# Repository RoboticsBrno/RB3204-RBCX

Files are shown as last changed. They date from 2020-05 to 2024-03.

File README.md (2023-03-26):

# RB3204-RBCX

<p align="center">




</p>

RBCX is a universal controller for hobby robots. It is a successor of [RB3201-RBControl](https://github.com/RoboticsBrno/RB3201-RBControl).
It is used in our robot [Robotka](https://robotka.robotickytabor.cz) on [Robo camp 2020](https://robotickytabor.cz).

<div align="center">
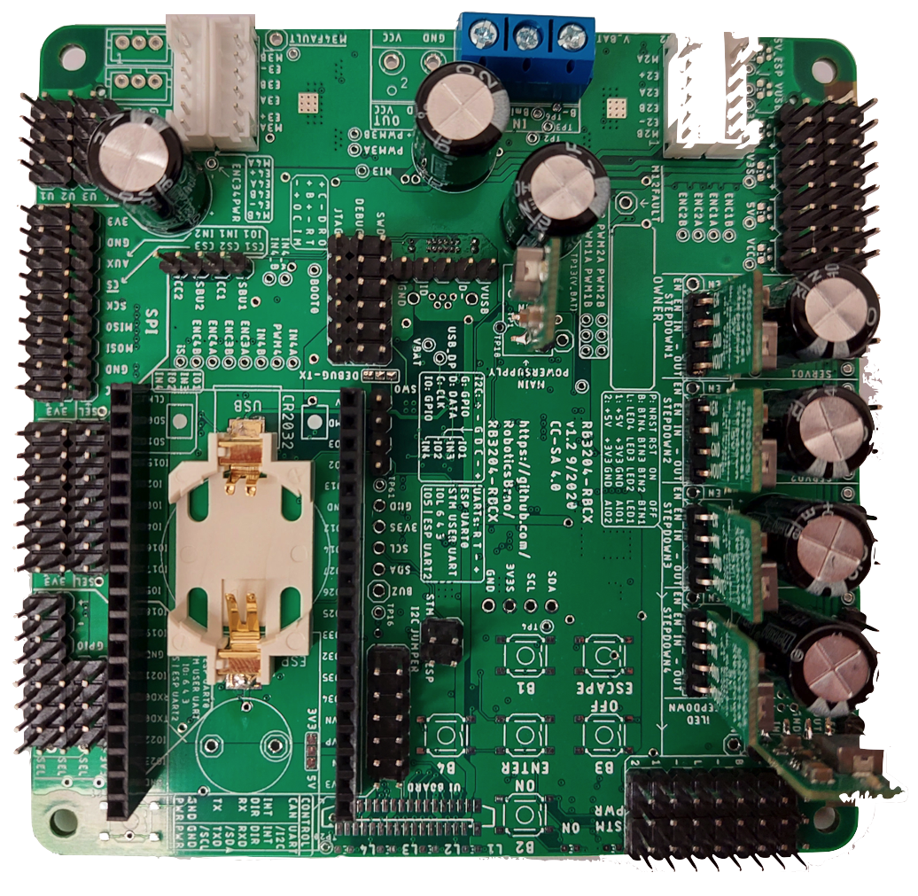
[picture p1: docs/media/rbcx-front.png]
  	<td></td>
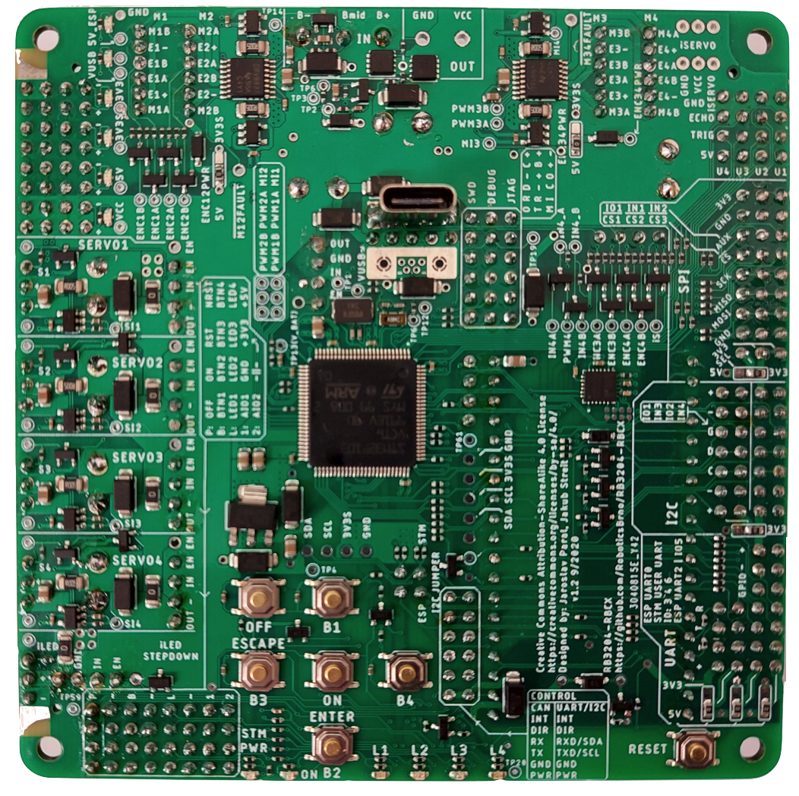
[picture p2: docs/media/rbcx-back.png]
	<td></td>
</div>

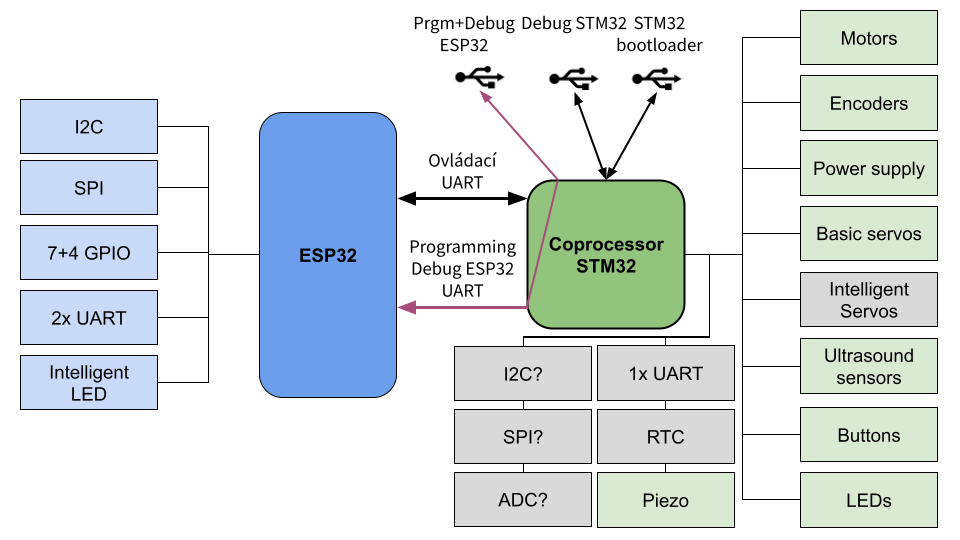
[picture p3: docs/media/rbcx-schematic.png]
RBCX


## Features
- 4 DC motors with encoders
- 4 servos with feedback (via ADC)
- 4 LEDs
- buttons with the gamepad interface
- Smart Servo connector
- piezo buzzer
- RTC
- ultra-sonic distance sensor connector
- I2C connectors
- OLED display connector
- accelerometer and gyroscope
- micro USB and USB-C connectors
- battery connector (without charging circuit)

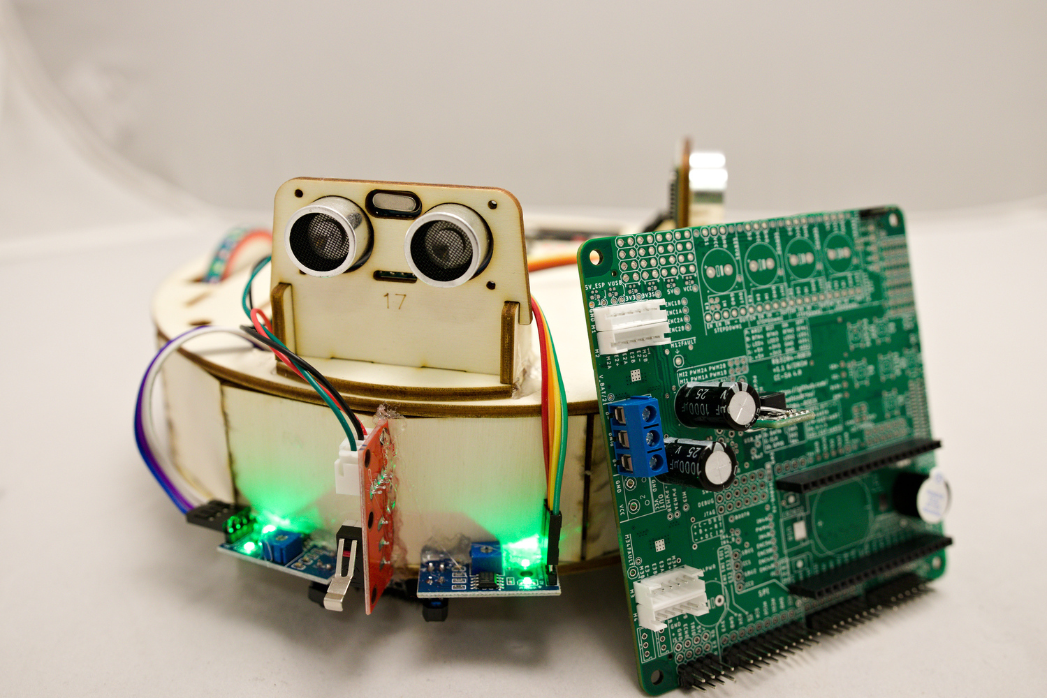
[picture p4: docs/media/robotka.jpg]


## Hardware
Board is based on `STM32F103VC` microcontroller and `ESP32-DevKitC`.

STM32 is used for motor control and other low-level tasks.
ESP32 is used for high-level tasks like communication with mobile app and sending commands to STM32 via UART.

### [STM32F103VC](https://www.st.com/en/microcontrollers-microprocessors/stm32f103vc.html)

-  72 MHz, 32bit ARM Cortex-M3
-  48 KiB RAM, 256 KiB Flash
-  5x UART, USB
-  Debug support (with ST-Link)
-  Programmable in C++, with FreeRTOS and stm32cube framework, in Platform.io
-  Our [bootloader](https://github.com/RoboticsBrno/sboot_stm32) based on [sboot_stm32](https://github.com/dmitrystu/sboot_stm32).

### [ESP32-DevKitC](https://www.espressif.com/en/products/devkits/esp32-devkitc)

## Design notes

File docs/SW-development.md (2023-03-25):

# Software development
Both microcontrollers are programmed using [PlatformIO](https://platformio.org/) in [VSCode](https://code.visualstudio.com/) using C++ language.

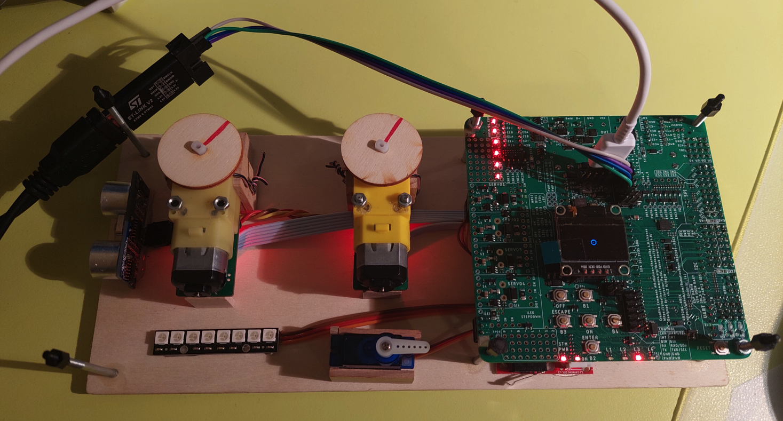
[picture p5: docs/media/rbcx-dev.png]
RBCX development


## STM32
The software for STM32 is located in `fw` directory.
STM32 uses our [bootloader](https://github.com/RoboticsBrno/sboot_stm32), which is based on [sboot_stm32](https://github.com/dmitrystu/sboot_stm32).

The Czech manuals are in these presentations:
- [RBCX](https://docs.google.com/presentation/d/1NP2yii9ZfLh_otC2qz9LTG4m3adRt0aGy-u8AYXcY6M/)
- [RBCX firmware](https://docs.google.com/presentation/d/1B4t7tvKhTz8Nwm9SQEp_2enkG-x4il2hApb1tdSRLiI)

### Bootloader installation
RBCX might work without bootloader, but it is not recommended. Thanls to the bootloader, you can program STM32 without STLink programmer and program ESP32 directly trough USB-C in RBCX.

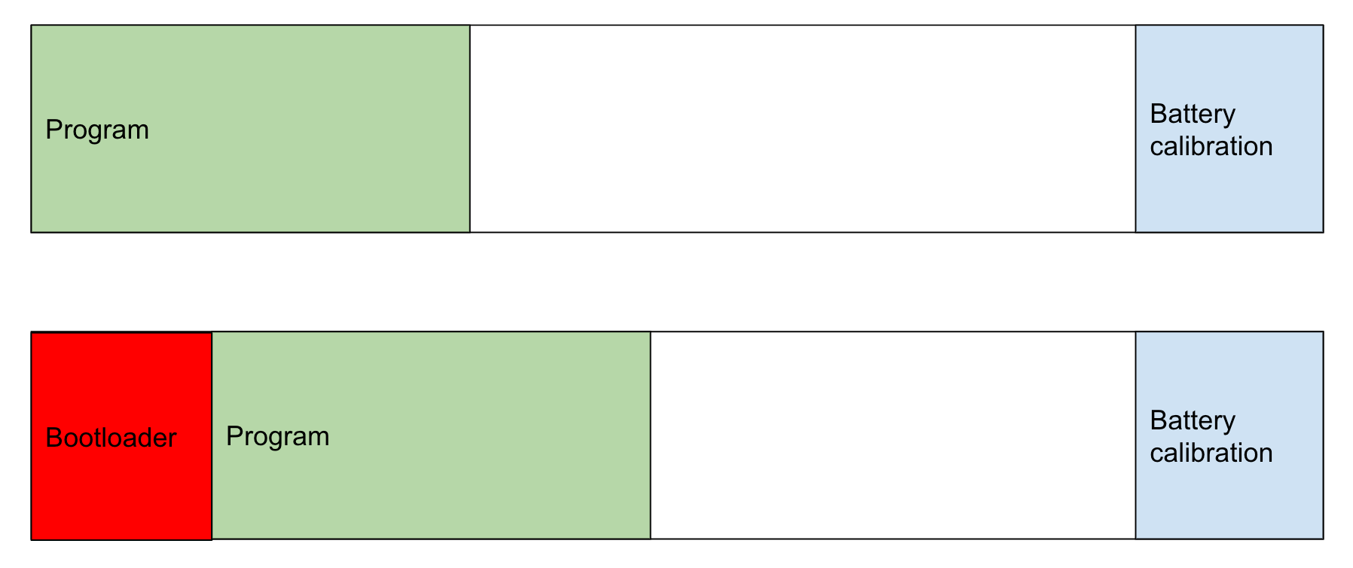
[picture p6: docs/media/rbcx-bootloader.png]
RBCX bootloader


- you need STLink programmer
  - connect STLink programmer to the board→
    - C → SWCLK
    - -→ GND
    - D → SWDIO
    - R → RST
    - +→ 3.3V (optional, if you want to power the board from STLink)
  - !! If STLink is not connected to the computer, STM32 is in a reset state !!
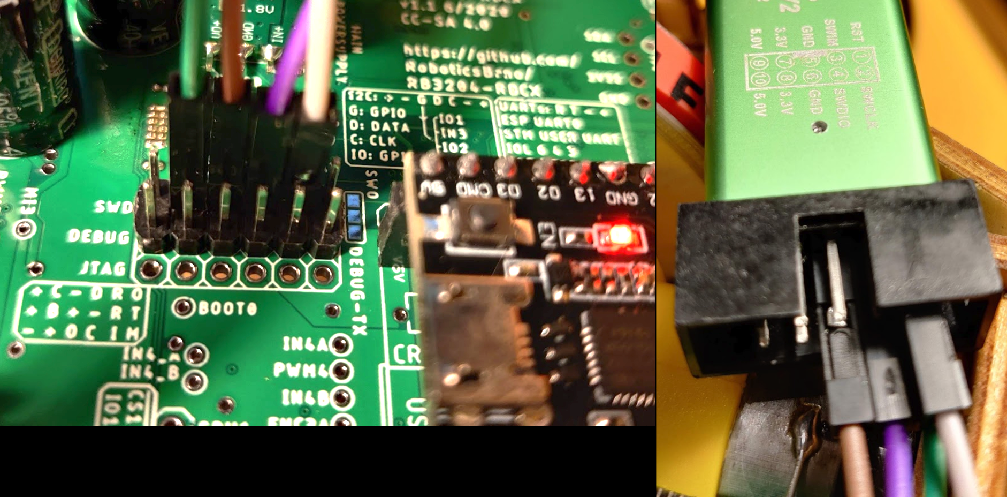
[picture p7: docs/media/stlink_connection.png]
STLink connection
  - 

- clone `https://github.com/RoboticsBrno/sboot_stm32`
- `apt-get install stlink-tools make gcc-arm-none-eabi git`
- flash prebuilt bootloader `st-flash --reset --format ihex write prebuilt/rbcx_v11/firmware.hex`
- compile and flash firmware `make prerequisites && ./rbcx_build_v11.sh && make program`

### Firmware installation
Firmware for STM32 is located in `fw/rbcx-coprocessor` directory.
RBCX might be programmed using STLink programmer or using USB-C connector.

### STLink development
In VSCode - PlatformIO, you have to change the environment to `hw*_stlink`.
This setup supports debugging. Just press `F5` or `Debug` button in VSCode.

### USB C development
If you want to use USB-C connector for programming STM32, you need to press `DOWN` button (B2) on the board during the boot.
In default mode, USB-C connector is used for communication with ESP32.

To enable Debug output from STM32, you have to press `LEFT` button (B3) on the board during the boot. This will add virtual debug serial port to the USB-C connector.

STM32 will create two virtual COM ports (one for STM32 and one for ESP32).
In VSCode - PlatformIO, you have to change the environment to `hw*_sboot`.
This setup does not support debugging (use STLink programmer for debugging).

## ESP32
The library for ESP32 is in [RB3204-RBCX-library](https://github.com/RoboticsBrno/RB3204-RBCX-library) repository.
Examples for the [Robotka](https://robotka.robotickytabor.cz), which is a robot based on RBCX, are in [robotka-examples](https://github.com/RoboticsBrno/robotka-examples) repository.

RBCX

## Programming ESP32
STM32 behaves like "FTDI" on dev kit, so you can program ESP32 using USB-C connector.

- Controls boot pins on ESP32 according to RTS/DTR.
- It supports faster UART than ESP32 DevKit (faster programming)
- ESP32 DevKit cannot be programmed via its own USB while plugged into RBCX

## ESP32 and STM32 communication
ESP32 and STM32 communicate via UART (baud 921600)

Microcontrollers are communicating using [Protocol Buffers](https://developers.google.com/protocol-buffers) (Protobuf).
Protobuf messages are defined in [RB3204-RBCX-coproc-comm](https://github.com/RoboticsBrno/RB3204-RBCX-coproc-comm) repository.

### Commands
"Run motor at 50%", "Battery voltage is 6802mV", "Reset the board"

Protocol: [Protobuf](https://protobuf.dev/) + [COBS](https://en.wikipedia.org/wiki/Consistent_Overhead_Byte_Stuffing) + small header

- `0x00, <length>, <data>`

Keepalive - when ESP32 does not respond, it is reset, STM32 turns off peripherals

### Installation and usage
- clone `https://github.com/RoboticsBrno/RB3204-RBCX-coproc-comm`
- install protobuf compiler `apt-get install protobuf-compiler`
- install nanopb generator `pip3 install nanopb==0.4.4`
- edit `rbcx.proto` file
- compile protobuf messages using `./generate.sh`
- commit and push changes to GitHub
- change GIT hash in FW and RBCX library to the latest commit hash

## Schematic
RBCX

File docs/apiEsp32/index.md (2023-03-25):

# API ESP-32

This is the API documentation for the [ESP32-DevKitC](https://www.espressif.com/en/products/devkits/esp32-devkitc) microcontroller.

## Firmware

More information about firmware can be found in [SW Development](../SW-development.md) section.

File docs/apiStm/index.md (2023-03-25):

# API STM32

This is the API documentation for the [STM32F103VC](https://www.st.com/en/microcontrollers-microprocessors/stm32f103vc.html) microcontroller.

## Firmware

More information about firmware can be found in [SW Development](../SW-development.md) section.

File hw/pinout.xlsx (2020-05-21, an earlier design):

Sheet: koprocesor
pin LQFP100 | 5V TOLERANT | GPIO | TIMER1 |  |  | TIMER2 |  |  |  | TIMER3 |  |  | TIMER4 |  | TIMER5 | TIMER8 | USART1 |  | USART2 |  | USART3 |  |  | UART4 | UART5 | CAN1 |  |  | I2C1 |  | I2C2 | SPI1 |  | SPI2 | SPI3 |  | USB | SDIO | DAC | ADC1 | ADC2 | ADC3 | JTAG/SWD | AUX | Periferie | Signal | Note
 |  | remap: | 00 | 01 | 11 | 00 | 01 | 10 | 11 | 00 | 10 | 11 | 0 | 1 |  |  | 0 | 1 | 0 | 1 | 00 | 01 | 11 |  |  | 00 | 10 | 11 | 0 | 1 |  | 0 | 1 |  | 0 | 1
1 |  | PE2 |  |  |  |  |  |  |  |  |  |  |  |  |  |  |  |  |  |  |  |  |  |  |  |  |  |  |  |  |  |  |  |  |  |  |  |  |  |  |  |  |  |  | PE2 | UTS2_TRIG
2 |  | PE3 |  |  |  |  |  |  |  |  |  |  |  |  |  |  |  |  |  |  |  |  |  |  |  |  |  |  |  |  |  |  |  |  |  |  |  |  |  |  |  |  |  |  | PE3 | UTS2_ECHO
3 |  | PE4 |  |  |  |  |  |  |  |  |  |  |  |  |  |  |  |  |  |  |  |  |  |  |  |  |  |  |  |  |  |  |  |  |  |  |  |  |  |  |  |  |  |  | PE4 | UTS3_TRIG
4 |  | PE5 |  |  |  |  |  |  |  |  |  |  |  |  |  |  |  |  |  |  |  |  |  |  |  |  |  |  |  |  |  |  |  |  |  |  |  |  |  |  |  |  |  |  | PE5 | UTS3_ECHO
5 |  | PE6 |  |  |  |  |  |  |  |  |  |  |  |  |  |  |  |  |  |  |  |  |  |  |  |  |  |  |  |  |  |  |  |  |  |  |  |  |  |  |  |  |  |  | PE6 | UTS4_TRIG
6 |  | VBAT |  |  |  |  |  |  |  |  |  |  |  |  |  |  |  |  |  |  |  |  |  |  |  |  |  |  |  |  |  |  |  |  |  |  |  |  |  |  |  |  |  |  | VBAT | VBAT
7 | LI+S | PC13 |  |  |  |  |  |  |  |  |  |  |  |  |  |  |  |  |  |  |  |  |  |  |  |  |  |  |  |  |  |  |  |  |  |  |  |  |  |  |  |  |  | RTC_TAMPER | PC13 | VUSB_DET
8 | LI+S | PC14 |  |  |  |  |  |  |  |  |  |  |  |  |  |  |  |  |  |  |  |  |  |  |  |  |  |  |  |  |  |  |  |  |  |  |  |  |  |  |  |  |  | OSC32_IN | OSC32_IN | OSC 32 kHz
9 | LI+S | PC15 |  |  |  |  |  |  |  |  |  |  |  |  |  |  |  |  |  |  |  |  |  |  |  |  |  |  |  |  |  |  |  |  |  |  |  |  |  |  |  |  |  | OSC32_OUT | OSC32_OUT | OSC 32 kHz
10 |  | VSS |  |  |  |  |  |  |  |  |  |  |  |  |  |  |  |  |  |  |  |  |  |  |  |  |  |  |  |  |  |  |  |  |  |  |  |  |  |  |  |  |  |  | VSS | VSS
11 |  | VDD |  |  |  |  |  |  |  |  |  |  |  |  |  |  |  |  |  |  |  |  |  |  |  |  |  |  |  |  |  |  |  |  |  |  |  |  |  |  |  |  |  |  | VDD | VDD
12 |  | OSC_IN |  |  |  |  |  |  |  |  |  |  |  |  |  |  |  |  |  |  |  |  |  |  |  |  |  |  |  |  |  |  |  |  |  |  |  |  |  |  |  |  |  |  | OSC_IN | OSC_IN
13 |  | OSC_OUT |  |  |  |  |  |  |  |  |  |  |  |  |  |  |  |  |  |  |  |  |  |  |  |  |  |  |  |  |  |  |  |  |  |  |  |  |  |  |  |  |  |  | OSC_OUT | OSC_OUT
14 |  | NRST |  |  |  |  |  |  |  |  |  |  |  |  |  |  |  |  |  |  |  |  |  |  |  |  |  |  |  |  |  |  |  |  |  |  |  |  |  |  |  |  |  |  | NRST | NRST
15 |  | PC0 |  |  |  |  |  |  |  |  |  |  |  |  |  |  |  |  |  |  |  |  |  |  |  |  |  |  |  |  |  |  |  |  |  |  |  |  |  | IN10 | IN10 | IN10 |  |  | ADC3_IN10 | SI1
16 |  | PC1 |  |  |  |  |  |  |  |  |  |  |  |  |  |  |  |  |  |  |  |  |  |  |  |  |  |  |  |  |  |  |  |  |  |  |  |  |  | IN11 | IN11 | IN11 |  |  | ADC3_IN11 | SI2
17 |  | PC2 |  |  |  |  |  |  |  |  |  |  |  |  |  |  |  |  |  |  |  |  |  |  |  |  |  |  |  |  |  |  |  |  |  |  |  |  |  | IN12 | IN12 | IN12 |  |  | ADC3_IN12 | SI3
18 |  | PC3 |  |  |  |  |  |  |  |  |  |  |  |  |  |  |  |  |  |  |  |  |  |  |  |  |  |  |  |  |  |  |  |  |  |  |  |  |  | IN13 | IN13 | IN13 |  |  | ADC3_IN13 | SI4
19 |  | VSSA |  |  |  |  |  |  |  |  |  |  |  |  |  |  |  |  |  |  |  |  |  |  |  |  |  |  |  |  |  |  |  |  |  |  |  |  |  |  |  |  |  |  | VSSA | VSSA
20 |  | VREF- |  |  |  |  |  |  |  |  |  |  |  |  |  |  |  |  |  |  |  |  |  |  |  |  |  |  |  |  |  |  |  |  |  |  |  |  |  |  |  |  |  |  | VREF- | VREF-
21 |  | VREF+ |  |  |  |  |  |  |  |  |  |  |  |  |  |  |  |  |  |  |  |  |  |  |  |  |  |  |  |  |  |  |  |  |  |  |  |  |  |  |  |  |  |  | VREF+ | VREF+
22 |  | VDDA |  |  |  |  |  |  |  |  |  |  |  |  |  |  |  |  |  |  |  |  |  |  |  |  |  |  |  |  |  |  |  |  |  |  |  |  |  |  |  |  |  |  | VDDA | VDDA
23 |  | PA0 |  |  |  | CH1_ETR |  | CH1_ETR |  |  |  |  |  |  | CH1 |  |  |  | CTS |  |  |  |  |  |  |  |  |  |  |  |  |  |  |  |  |  |  |  |  | IN0 | IN0 | IN0 |  | WKUP | TIM5_CH1 | SERVO1
24 |  | PA1 |  |  |  | CH2 |  | CH2 |  |  |  |  |  |  | CH2 |  |  |  | RTS |  |  |  |  |  |  |  |  |  |  |  |  |  |  |  |  |  |  |  |  | IN1 | IN1 | IN1 |  |  | TIM5_CH2 | SERVO2
25 |  | PA2 |  |  |  | CH3 | CH3 |  |  |  |  |  |  |  | CH3 |  |  |  | TX |  |  |  |  |  |  |  |  |  |  |  |  |  |  |  |  |  |  |  |  | IN2 | IN2 | IN2 |  |  | TIM5_CH3 | SERVO3
26 |  | PA3 |  |  |  | CH4 | CH4 |  |  |  |  |  |  |  | CH4 |  |  |  | RX |  |  |  |  |  |  |  |  |  |  |  |  |  |  |  |  |  |  |  |  | IN3 | IN3 | IN3 |  |  | TIM5_CH4 | SERVO4
27 |  | VSS |  |  |  |  |  |  |  |  |  |  |  |  |  |  |  |  |  |  |  |  |  |  |  |  |  |  |  |  |  |  |  |  |  |  |  |  |  |  |  |  |  |  | VSS | VSS
28 |  | VDD |  |  |  |  |  |  |  |  |  |  |  |  |  |  |  |  |  |  |  |  |  |  |  |  |  |  |  |  |  |  |  |  |  |  |  |  |  |  |  |  |  |  | VDD | VDD
29 |  | PA4 |  |  |  |  |  |  |  |  |  |  |  |  |  |  |  |  | CK |  |  |  |  |  |  |  |  |  |  |  |  | NSS |  |  |  | NSS |  |  | OUT1 | IN4 | IN4 |  |  |  | DAC1/ADC2_IN4 | AIO4
30 |  | PA5 |  |  |  |  |  |  |  |  |  |  |  |  |  |  |  |  |  |  |  |  |  |  |  |  |  |  |  |  |  | SCK |  |  |  |  |  |  | OUT2 | IN5 | IN5 |  |  |  | DAC2/ADC2_IN5 | AIO5
31 |  | PA6 |  | BKIN |  |  |  |  |  | CH1 |  |  |  |  |  | BKIN |  |  |  |  |  |  |  |  |  |  |  |  |  |  |  | MISO |  |  |  |  |  |  |  | IN6 | IN6 |  |  |  | ADC2_IN6 | VBAT
32 |  | PA7 |  | CH1N |  |  |  |  |  | CH2 |  |  |  |  |  | CH1N |  |  |  |  |  |  |  |  |  |  |  |  |  |  |  | MOSI |  |  |  |  |  |  |  | IN7 | IN7 |  |  |  | ADC2_IN7 | VBAT/2
33 |  | PC4 |  |  |  |  |  |  |  |  |  |  |  |  |  |  |  |  |  |  |  |  |  |  |  |  |  |  |  |  |  |  |  |  |  |  |  |  |  | IN14 | IN14 |  |  |  | ADC1_IN14 | MI1
34 |  | PC5 |  |  |  |  |  |  |  |  |  |  |  |  |  |  |  |  |  |  |  |  |  |  |  |  |  |  |  |  |  |  |  |  |  |  |  |  |  | IN15 | IN15 |  |  |  | ADC1_IN15 | MI2
35 |  | PB0 |  | CH2N |  |  |  |  |  | CH3 | CH3 |  |  |  |  | CH2N |  |  |  |  |  |  |  |  |  |  |  |  |  |  |  |  |  |  |  |  |  |  |  | IN8 | IN8 |  |  |  | ADC1_IN8 | MI3
36 |  | PB1 |  | CH3N |  |  |  |  |  | CH4 | CH4 |  |  |  |  | CH3N |  |  |  |  |  |  |  |  |  |  |  |  |  |  |  |  |  |  |  |  |  |  |  | IN9 | IN9 |  |  |  | ADC1_IN9 | MI4
37 |  | PB2 |  |  |  |  |  |  |  |  |  |  |  |  |  |  |  |  |  |  |  |  |  |  |  |  |  |  |  |  |  |  |  |  |  |  |  |  |  |  |  |  |  | BOOT1 | PB2 | BUTTON3
38 |  | PE7 |  |  | ETR |  |  |  |  |  |  |  |  |  |  |  |  |  |  |  |  |  |  |  |  |  |  |  |  |  |  |  |  |  |  |  |  |  |  |  |  |  |  |  | PE7 | UTS4_ECHO
39 |  | PE8 |  |  | CH1N |  |  |  |  |  |  |  |  |  |  |  |  |  |  |  |  |  |  |  |  |  |  |  |  |  |  |  |  |  |  |  |  |  |  |  |  |  |  |  | CH1N | PWM1B
40 |  | PE9 |  |  | CH1 |  |  |  |  |  |  |  |  |  |  |  |  |  |  |  |  |  |  |  |  |  |  |  |  |  |  |  |  |  |  |  |  |  |  |  |  |  |  |  | CH1 | PWM1A
41 |  | PE10 |  |  | CH2N |  |  |  |  |  |  |  |  |  |  |  |  |  |  |  |  |  |  |  |  |  |  |  |  |  |  |  |  |  |  |  |  |  |  |  |  |  |  |  | CH2N | PWM2B
42 |  | PE11 |  |  | CH2 |  |  |  |  |  |  |  |  |  |  |  |  |  |  |  |  |  |  |  |  |  |  |  |  |  |  |  |  |  |  |  |  |  |  |  |  |  |  |  | CH2 | PWM2A
43 |  | PE12 |  |  | CH3N |  |  |  |  |  |  |  |  |  |  |  |  |  |  |  |  |  |  |  |  |  |  |  |  |  |  |  |  |  |  |  |  |  |  |  |  |  |  |  | CH3N | PWM3B
44 |  | PE13 |  |  | CH3 |  |  |  |  |  |  |  |  |  |  |  |  |  |  |  |  |  |  |  |  |  |  |  |  |  |  |  |  |  |  |  |  |  |  |  |  |  |  |  | CH3 | PWM3A
45 |  | PE14 |  |  | CH4 |  |  |  |  |  |  |  |  |  |  |  |  |  |  |  |  |  |  |  |  |  |  |  |  |  |  |  |  |  |  |  |  |  |  |  |  |  |  |  | CH4 | PWM4
46 |  | PE15 |  |  | BKIN |  |  |  |  |  |  |  |  |  |  |  |  |  |  |  |  |  |  |  |  |  |  |  |  |  |  |  |  |  |  |  |  |  |  |  |  |  |  |  | PE15/TIM1_BKIN | BUTTON_ESC/OFF
47 |  | PB10 |  |  |  |  |  | CH3 | CH3 |  |  |  |  |  |  |  |  |  |  |  | TX |  |  |  |  |  |  |  |  |  | SCL |  |  |  |  |  |  |  |  |  |  |  |  |  | I2C2_SCL | I2C_SCL
48 |  | PB11 |  |  |  |  |  | CH4 | CH4 |  |  |  |  |  |  |  |  |  |  |  | RX |  |  |  |  |  |  |  |  |  | SDA |  |  |  |  |  |  |  |  |  |  |  |  |  | I2C2_SDA | I2C_SDA
49 |  | VSS |  |  |  |  |  |  |  |  |  |  |  |  |  |  |  |  |  |  |  |  |  |  |  |  |  |  |  |  |  |  |  |  |  |  |  |  |  |  |  |  |  |  | VSS | VSS
50 |  | VDD |  |  |  |  |  |  |  |  |  |  |  |  |  |  |  |  |  |  |  |  |  |  |  |  |  |  |  |  |  |  |  |  |  |  |  |  |  |  |  |  |  |  | VDD | VDD
51 |  | PB12 | BKIN |  |  |  |  |  |  |  |  |  |  |  |  |  |  |  |  |  | CK |  |  |  |  |  |  |  |  |  | SMBA |  |  | NSS |  |  |  |  |  |  |  |  |  |  | SPI2_NSS | SPI/ESP_JTAG
52 |  | PB13 | CH1N |  |  |  |  |  |  |  |  |  |  |  |  |  |  |  |  |  | CTS | CTS |  |  |  |  |  |  |  |  |  |  |  | SCK |  |  |  |  |  |  |  |  |  |  | SPI2_SCK | SPI/ESP_JTAG
53 |  | PB14 | CH2N |  |  |  |  |  |  |  |  |  |  |  |  |  |  |  |  |  | RTS | RTS |  |  |  |  |  |  |  |  |  |  |  | MISO |  |  |  |  |  |  |  |  |  |  | SPI2_MISO | SPI/ESP_JTAG
54 |  | PB15 | CH3N |  |  |  |  |  |  |  |  |  |  |  |  |  |  |  |  |  |  |  |  |  |  |  |  |  |  |  |  |  |  | MOSI |  |  |  |  |  |  |  |  |  |  | SPI2_MOSI | SPI/ESP_JTAG
55 |  | PD8 |  |  |  |  |  |  |  |  |  |  |  |  |  |  |  |  |  |  |  |  | TX |  |  |  |  |  |  |  |  |  |  |  |  |  |  |  |  |  |  |  |  |  | USART3_TX/RX | INTELLIGENT_SERVO
56 |  | PD9 |  |  |  |  |  |  |  |  |  |  |  |  |  |  |  |  |  |  |  |  | RX |  |  |  |  |  |  |  |  |  |  |  |  |  |  |  |  |  |  |  |  |  | PD9 | POWER
57 |  | PD10 |  |  |  |  |  |  |  |  |  |  |  |  |  |  |  |  |  |  |  |  | CK |  |  |  |  |  |  |  |  |  |  |  |  |  |  |  |  |  |  |  |  |  | PD10 | LED1
58 |  | PD11 |  |  |  |  |  |  |  |  |  |  |  |  |  |  |  |  |  |  |  |  | CTS |  |  |  |  |  |  |  |  |  |  |  |  |  |  |  |  |  |  |  |  |  | PD11 | LED2
59 |  | PD12 |  |  |  |  |  |  |  |  |  |  |  | CH1 |  |  |  |  |  |  |  |  | RTS |  |  |  |  |  |  |  |  |  |  |  |  |  |  |  |  |  |  |  |  |  | TIM4_CH1 | ENC3A
60 |  | PD13 |  |  |  |  |  |  |  |  |  |  |  | CH2 |  |  |  |  |  |  |  |  |  |  |  |  |  |  |  |  |  |  |  |  |  |  |  |  |  |  |  |  |  |  | TIM4_CH2 | ENC3B
61 |  | PD14 |  |  |  |  |  |  |  |  |  |  |  | CH3 |  |  |  |  |  |  |  |  |  |  |  |  |  |  |  |  |  |  |  |  |  |  |  |  |  |  |  |  |  |  | PD14 | LED3
62 |  | PD15 |  |  |  |  |  |  |  |  |  |  |  | CH4 |  |  |  |  |  |  |  |  |  |  |  |  |  |  |  |  |  |  |  |  |  |  |  |  |  |  |  |  |  |  | PD15 | LED4
63 |  | PC6 |  |  |  |  |  |  |  |  |  | CH1 |  |  |  | CH1 |  |  |  |  |  |  |  |  |  |  |  |  |  |  |  |  |  |  |  |  |  | D6 |  |  |  |  |  |  | TIM8_CH1 | ENC4A
64 |  | PC7 |  |  |  |  |  |  |  |  |  | CH2 |  |  |  | CH2 |  |  |  |  |  |  |  |  |  |  |  |  |  |  |  |  |  |  |  |  |  | D7 |  |  |  |  |  |  | TIM8_CH2 | ENC4B
65 |  | PC8 |  |  |  |  |  |  |  |  |  | CH3 |  |  |  | CH3 |  |  |  |  |  |  |  |  |  |  |  |  |  |  |  |  |  |  |  |  |  | D0 |  |  |  |  |  |  | PC8 | ESP_EN
66 |  | PC9 |  |  |  |  |  |  |  |  |  | CH4 |  |  |  | CH4 |  |  |  |  |  |  |  |  |  |  |  |  |  |  |  |  |  |  |  |  |  | D1 |  |  |  |  |  |  | PC9 | BUTTON_ON
67 |  | PA8 | CH1 | CH1 |  |  |  |  |  |  |  |  |  |  |  |  | CK | CK |  |  |  |  |  |  |  |  |  |  |  |  |  |  |  |  |  |  |  |  |  |  |  |  |  | MCO | PA8 | USB_DP_PULLUP
68 |  | PA9 | CH2 | CH2 |  |  |  |  |  |  |  |  |  |  |  |  | TX |  |  |  |  |  |  |  |  |  |  |  |  |  |  |  |  |  |  |  |  |  |  |  |  |  |  |  | USART1_TX | DEBUG
69 |  | PA10 | CH3 | CH3 |  |  |  |  |  |  |  |  |  |  |  |  | RX |  |  |  |  |  |  |  |  |  |  |  |  |  |  |  |  |  |  |  |  |  |  |  |  |  |  |  | USART1_RX | DEBUG
70 |  | PA11 | CH4 | CH4 |  |  |  |  |  |  |  |  |  |  |  |  | CTS | CTS |  |  |  |  |  |  |  | RX |  |  |  |  |  |  |  |  |  |  | DM |  |  |  |  |  |  |  | USB_DM | USB
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

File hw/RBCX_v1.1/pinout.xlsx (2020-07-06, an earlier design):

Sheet: koprocesor
pin LQFP100 | 5V TOLERANT | GPIO | TIMER1 |  |  | TIMER2 |  |  |  | TIMER3 |  |  | TIMER4 |  | TIMER5 | TIMER8 | USART1 |  | USART2 |  | USART3 |  |  | UART4 | UART5 | CAN1 |  |  | I2C1 |  | I2C2 | SPI1 |  | SPI2 | SPI3 |  | USB | SDIO | DAC | ADC1 | ADC2 | ADC3 | JTAG/SWD | AUX | GPIO | Periferie | Signal | Interrupt | Note
 |  | remap: | 00 | 01 | 11 | 00 | 01 | 10 | 11 | 00 | 10 | 11 | 0 | 1 |  |  | 0 | 1 | 0 | 1 | 00 | 01 | 11 |  |  | 00 | 10 | 11 | 0 | 1 |  | 0 | 1 |  | 0 | 1
1 |  | PE2 |  |  |  |  |  |  |  |  |  |  |  |  |  |  |  |  |  |  |  |  |  |  |  |  |  |  |  |  |  |  |  |  |  |  |  |  |  |  |  |  |  |  | PE2 | PE2 | UTS2_TRIG |  |  | Summary:
2 |  | PE3 |  |  |  |  |  |  |  |  |  |  |  |  |  |  |  |  |  |  |  |  |  |  |  |  |  |  |  |  |  |  |  |  |  |  |  |  |  |  |  |  |  |  | PE3 | PE3 | UTS3_TRIG |  |  |  | 0 | 1 | 2 | 3 | 4 | 5 | 6
3 |  | PE4 |  |  |  |  |  |  |  |  |  |  |  |  |  |  |  |  |  |  |  |  |  |  |  |  |  |  |  |  |  |  |  |  |  |  |  |  |  |  |  |  |  |  | PE4 | PE4 | UTS4_TRIG |  |  | A | ENC2A | ENC2B | VUSB_DET | VBAT/2 | AIO1 | AIO2 | VBAT
4 |  | PE5 |  |  |  |  |  |  |  |  |  |  |  |  |  |  |  |  |  |  |  |  |  |  |  |  |  |  |  |  |  |  |  |  |  |  |  |  |  |  |  |  |  |  | PE5 | PE5 | IN4A |  |  | B | MI3 | MI4 | BUTTON3 | ENC3B | ENC4A | ENC4B | USER_TX
5 |  | PE6 |  |  |  |  |  |  |  |  |  |  |  |  |  |  |  |  |  |  |  |  |  |  |  |  |  |  |  |  |  |  |  |  |  |  |  |  |  |  |  |  |  |  | PE6 | PE6 | UTS1_ECHO | 6 |  | C | SI4 | SI3 | SI2 | SI1 | MI1 | MI2 | SERVO1
6 |  | VBAT |  |  |  |  |  |  |  |  |  |  |  |  |  |  |  |  |  |  |  |  |  |  |  |  |  |  |  |  |  |  |  |  |  |  |  |  |  |  |  |  |  |  | VBAT | VBAT | VBAT |  |  | D | CAN_RX | CAN_TX | USB_DP_PULLUP | BUZZER | ESP_EN | TUNNEL_TX | TUNNEL_RX
7 | LI+S | PC13 |  |  |  |  |  |  |  |  |  |  |  |  |  |  |  |  |  |  |  |  |  |  |  |  |  |  |  |  |  |  |  |  |  |  |  |  |  |  |  |  |  | RTC_TAMPER | PC13 | PC13 | POWER |  |  | E | BUTTON1 | UTS1_TRIG | UTS2_TRIG | UTS3_TRIG | UTS4_TRIG | IN4A | UTS1_ECHO
8 | LI+S | PC14 |  |  |  |  |  |  |  |  |  |  |  |  |  |  |  |  |  |  |  |  |  |  |  |  |  |  |  |  |  |  |  |  |  |  |  |  |  |  |  |  |  | OSC32_IN | PC14 | OSC32_IN | OSC32_IN |  |  |  | INTERRUPT
9 | LI+S | PC15 |  |  |  |  |  |  |  |  |  |  |  |  |  |  |  |  |  |  |  |  |  |  |  |  |  |  |  |  |  |  |  |  |  |  |  |  |  |  |  |  |  | OSC32_OUT | PC15 | OSC32_OUT | OSC32_OUT |  |  |  | BUTTON1 | ENC2B | BUTTON2 | ENC3B | ESP_EN | ENC4B | UTS1_ECHO
10 |  | VSS |  |  |  |  |  |  |  |  |  |  |  |  |  |  |  |  |  |  |  |  |  |  |  |  |  |  |  |  |  |  |  |  |  |  |  |  |  |  |  |  |  |  | VSS | VSS | VSS
11 |  | VDD |  |  |  |  |  |  |  |  |  |  |  |  |  |  |  |  |  |  |  |  |  |  |  |  |  |  |  |  |  |  |  |  |  |  |  |  |  |  |  |  |  |  | VDD | VDD | VDD
12 |  | OSC_IN |  |  |  |  |  |  |  |  |  |  |  |  |  |  |  |  |  |  |  |  |  |  |  |  |  |  |  |  |  |  |  |  |  |  |  |  |  |  |  |  |  |  | OSC_IN | OSC_IN | OSC_IN
13 |  | OSC_OUT |  |  |  |  |  |  |  |  |  |  |  |  |  |  |  |  |  |  |  |  |  |  |  |  |  |  |  |  |  |  |  |  |  |  |  |  |  |  |  |  |  |  | OSC_OUT | OSC_OUT | OSC_OUT
14 |  | NRST |  |  |  |  |  |  |  |  |  |  |  |  |  |  |  |  |  |  |  |  |  |  |  |  |  |  |  |  |  |  |  |  |  |  |  |  |  |  |  |  |  |  | NRST | NRST | NRST
15 |  | PC0 |  |  |  |  |  |  |  |  |  |  |  |  |  |  |  |  |  |  |  |  |  |  |  |  |  |  |  |  |  |  |  |  |  |  |  |  |  | IN10 | IN10 | IN10 |  |  | PC0 | ADC3_IN10 | SI4
16 |  | PC1 |  |  |  |  |  |  |  |  |  |  |  |  |  |  |  |  |  |  |  |  |  |  |  |  |  |  |  |  |  |  |  |  |  |  |  |  |  | IN11 | IN11 | IN11 |  |  | PC1 | ADC3_IN11 | SI3
17 |  | PC2 |  |  |  |  |  |  |  |  |  |  |  |  |  |  |  |  |  |  |  |  |  |  |  |  |  |  |  |  |  |  |  |  |  |  |  |  |  | IN12 | IN12 | IN12 |  |  | PC2 | ADC3_IN12 | SI2
18 |  | PC3 |  |  |  |  |  |  |  |  |  |  |  |  |  |  |  |  |  |  |  |  |  |  |  |  |  |  |  |  |  |  |  |  |  |  |  |  |  | IN13 | IN13 | IN13 |  |  | PC3 | ADC3_IN13 | SI1
19 |  | VSSA |  |  |  |  |  |  |  |  |  |  |  |  |  |  |  |  |  |  |  |  |  |  |  |  |  |  |  |  |  |  |  |  |  |  |  |  |  |  |  |  |  |  | VSSA | VSSA | VSSA
20 |  | VREF- |  |  |  |  |  |  |  |  |  |  |  |  |  |  |  |  |  |  |  |  |  |  |  |  |  |  |  |  |  |  |  |  |  |  |  |  |  |  |  |  |  |  | VREF- | VREF- | VREF-
21 |  | VREF+ |  |  |  |  |  |  |  |  |  |  |  |  |  |  |  |  |  |  |  |  |  |  |  |  |  |  |  |  |  |  |  |  |  |  |  |  |  |  |  |  |  |  | VREF+ | VREF+ | VREF+
22 |  | VDDA |  |  |  |  |  |  |  |  |  |  |  |  |  |  |  |  |  |  |  |  |  |  |  |  |  |  |  |  |  |  |  |  |  |  |  |  |  |  |  |  |  |  | VDDA | VDDA | VDDA
23 |  | PA0 |  |  |  | CH1_ETR |  | CH1_ETR |  |  |  |  |  |  | CH1 |  |  |  | CTS |  |  |  |  |  |  |  |  |  |  |  |  |  |  |  |  |  |  |  |  | IN0 | IN0 | IN0 |  | WKUP | PA0 | TIM5_CH1 | ENC2A
24 |  | PA1 |  |  |  | CH2 |  | CH2 |  |  |  |  |  |  | CH2 |  |  |  | RTS |  |  |  |  |  |  |  |  |  |  |  |  |  |  |  |  |  |  |  |  | IN1 | IN1 | IN1 |  |  | PA1 | TIM5_CH2 | ENC2B | 1
25 |  | PA2 |  |  |  | CH3 | CH3 |  |  |  |  |  |  |  | CH3 |  |  |  | TX |  |  |  |  |  |  |  |  |  |  |  |  |  |  |  |  |  |  |  |  | IN2 | IN2 | IN2 |  |  | PA2 | PA2/ADC1_IN2 | VUSB_DET
26 |  | PA3 |  |  |  | CH4 | CH4 |  |  |  |  |  |  |  | CH4 |  |  |  | RX |  |  |  |  |  |  |  |  |  |  |  |  |  |  |  |  |  |  |  |  | IN3 | IN3 | IN3 |  |  | PA3 | ADC1_IN3 | VBAT/2
27 |  | VSS |  |  |  |  |  |  |  |  |  |  |  |  |  |  |  |  |  |  |  |  |  |  |  |  |  |  |  |  |  |  |  |  |  |  |  |  |  |  |  |  |  |  | VSS | VSS | VSS
28 |  | VDD |  |  |  |  |  |  |  |  |  |  |  |  |  |  |  |  |  |  |  |  |  |  |  |  |  |  |  |  |  |  |  |  |  |  |  |  |  |  |  |  |  |  | VDD | VDD | VDD
29 |  | PA4 |  |  |  |  |  |  |  |  |  |  |  |  |  |  |  |  | CK |  |  |  |  |  |  |  |  |  |  |  |  | NSS |  |  |  | NSS |  |  | OUT1 | IN4 | IN4 |  |  |  | PA4 | DAC1/ADC2_IN4 | AIO1
30 |  | PA5 |  |  |  |  |  |  |  |  |  |  |  |  |  |  |  |  |  |  |  |  |  |  |  |  |  |  |  |  |  | SCK |  |  |  |  |  |  | OUT2 | IN5 | IN5 |  |  |  | PA5 | DAC2/ADC2_IN5 | AIO2
31 |  | PA6 |  | BKIN |  |  |  |  |  | CH1 |  |  |  |  |  | BKIN |  |  |  |  |  |  |  |  |  |  |  |  |  |  |  | MISO |  |  |  |  |  |  |  | IN6 | IN6 |  |  |  | PA6 | ADC2_IN6 | VBAT
32 |  | PA7 |  | CH1N |  |  |  |  |  | CH2 |  |  |  |  |  | CH1N |  |  |  |  |  |  |  |  |  |  |  |  |  |  |  | MOSI |  |  |  |  |  |  |  | IN7 | IN7 |  |  |  | PA7 | PA7 | LED1
33 |  | PC4 |  |  |  |  |  |  |  |  |  |  |  |  |  |  |  |  |  |  |  |  |  |  |  |  |  |  |  |  |  |  |  |  |  |  |  |  |  | IN14 | IN14 |  |  |  | PC4 | ADC1_IN14 | MI1
34 |  | PC5 |  |  |  |  |  |  |  |  |  |  |  |  |  |  |  |  |  |  |  |  |  |  |  |  |  |  |  |  |  |  |  |  |  |  |  |  |  | IN15 | IN15 |  |  |  | PC5 | ADC1_IN15 | MI2
35 |  | PB0 |  | CH2N |  |  |  |  |  | CH3 | CH3 |  |  |  |  | CH2N |  |  |  |  |  |  |  |  |  |  |  |  |  |  |  |  |  |  |  |  |  |  |  | IN8 | IN8 |  |  |  | PB0 | ADC1_IN8 | MI3
36 |  | PB1 |  | CH3N |  |  |  |  |  | CH4 | CH4 |  |  |  |  | CH3N |  |  |  |  |  |  |  |  |  |  |  |  |  |  |  |  |  |  |  |  |  |  |  | IN9 | IN9 |  |  |  | PB1 | ADC1_IN9 | MI4
37 |  | PB2 |  |  |  |  |  |  |  |  |  |  |  |  |  |  |  |  |  |  |  |  |  |  |  |  |  |  |  |  |  |  |  |  |  |  |  |  |  |  |  |  |  | BOOT1 | PB2 | PB2 | BUTTON3 | 2
38 |  | PE7 |  |  | ETR |  |  |  |  |  |  |  |  |  |  |  |  |  |  |  |  |  |  |  |  |  |  |  |  |  |  |  |  |  |  |  |  |  |  |  |  |  |  |  | PE7 | PE7 | IN4B
39 |  | PE8 |  |  | CH1N |  |  |  |  |  |  |  |  |  |  |  |  |  |  |  |  |  |  |  |  |  |  |  |  |  |  |  |  |  |  |  |  |  |  |  |  |  |  |  | PE8 | CH1N | PWM1B
40 |  | PE9 |  |  | CH1 |  |  |  |  |  |  |  |  |  |  |  |  |  |  |  |  |  |  |  |  |  |  |  |  |  |  |  |  |  |  |  |  |  |  |  |  |  |  |  | PE9 | CH1 | PWM1A
41 |  | PE10 |  |  | CH2N |  |  |  |  |  |  |  |  |  |  |  |  |  |  |  |  |  |  |  |  |  |  |  |  |  |  |  |  |  |  |  |  |  |  |  |  |  |  |  | PE10 | CH2N | PWM2B
42 |  | PE11 |  |  | CH2 |  |  |  |  |  |  |  |  |  |  |  |  |  |  |  |  |  |  |  |  |  |  |  |  |  |  |  |  |  |  |  |  |  |  |  |  |  |  |  | PE11 | CH2 | PWM2A
43 |  | PE12 |  |  | CH3N |  |  |  |  |  |  |  |  |  |  |  |  |  |  |  |  |  |  |  |  |  |  |  |  |  |  |  |  |  |  |  |  |  |  |  |  |  |  |  | PE12 | CH3N | PWM3B
44 |  | PE13 |  |  | CH3 |  |  |  |  |  |  |  |  |  |  |  |  |  |  |  |  |  |  |  |  |  |  |  |  |  |  |  |  |  |  |  |  |  |  |  |  |  |  |  | PE13 | CH3 | PWM3A
45 |  | PE14 |  |  | CH4 |  |  |  |  |  |  |  |  |  |  |  |  |  |  |  |  |  |  |  |  |  |  |  |  |  |  |  |  |  |  |  |  |  |  |  |  |  |  |  | PE14 | CH4 | PWM4
46 |  | PE15 |  |  | BKIN |  |  |  |  |  |  |  |  |  |  |  |  |  |  |  |  |  |  |  |  |  |  |  |  |  |  |  |  |  |  |  |  |  |  |  |  |  |  |  | PE15 | PE15/TIM1_BKIN | BUTTON_OFF | 15
47 |  | PB10 |  |  |  |  |  | CH3 | CH3 |  |  |  |  |  |  |  |  |  |  |  | TX |  |  |  |  |  |  |  |  |  | SCL |  |  |  |  |  |  |  |  |  |  |  |  |  | PB10 | USART3_TX | CONTROL_TX
48 |  | PB11 |  |  |  |  |  | CH4 | CH4 |  |  |  |  |  |  |  |  |  |  |  | RX |  |  |  |  |  |  |  |  |  | SDA |  |  |  |  |  |  |  |  |  |  |  |  |  | PB11 | USART3_RX | CONTROL_RX
49 |  | VSS |  |  |  |  |  |  |  |  |  |  |  |  |  |  |  |  |  |  |  |  |  |  |  |  |  |  |  |  |  |  |  |  |  |  |  |  |  |  |  |  |  |  | VSS | VSS | VSS
50 |  | VDD |  |  |  |  |  |  |  |  |  |  |  |  |  |  |  |  |  |  |  |  |  |  |  |  |  |  |  |  |  |  |  |  |  |  |  |  |  |  |  |  |  |  | VDD | VDD | VDD
51 |  | PB12 | BKIN |  |  |  |  |  |  |  |  |  |  |  |  |  |  |  |  |  | CK |  |  |  |  |  |  |  |  |  | SMBA |  |  | NSS |  |  |  |  |  |  |  |  |  |  | PB12 | SPI2_NSS | SPI/ESP_JTAG
52 |  | PB13 | CH1N |  |  |  |  |  |  |  |  |  |  |  |  |  |  |  |  |  | CTS | CTS |  |  |  |  |  |  |  |  |  |  |  | SCK |  |  |  |  |  |  |  |  |  |  | PB13 | SPI2_SCK | SPI/ESP_JTAG
53 |  | PB14 | CH2N |  |  |  |  |  |  |  |  |  |  |  |  |  |  |  |  |  | RTS | RTS |  |  |  |  |  |  |  |  |  |  |  | MISO |  |  |  |  |  |  |  |  |  |  | PB14 | SPI2_MISO | SPI/ESP_JTAG
54 |  | PB15 | CH3N |  |  |  |  |  |  |  |  |  |  |  |  |  |  |  |  |  |  |  |  |  |  |  |  |  |  |  |  |  |  | MOSI |  |  |  |  |  |  |  |  |  |  | PB15 | SPI2_MOSI | SPI/ESP_JTAG
55 |  | PD8 |  |  |  |  |  |  |  |  |  |  |  |  |  |  |  |  |  |  |  |  | TX |  |  |  |  |  |  |  |  |  |  |  |  |  |  |  |  |  |  |  |  |  | PD8 | PD8 | UTS3_ECHO | 8
56 |  | PD9 |  |  |  |  |  |  |  |  |  |  |  |  |  |  |  |  |  |  |  |  | RX |  |  |  |  |  |  |  |  |  |  |  |  |  |  |  |  |  |  |  |  |  | PD9 | PD9 | UTS4_ECHO | 9
57 |  | PD10 |  |  |  |  |  |  |  |  |  |  |  |  |  |  |  |  |  |  |  |  | CK |  |  |  |  |  |  |  |  |  |  |  |  |  |  |  |  |  |  |  |  |  | PD10 | PD10 | BUTTON2 | 10
58 |  | PD11 |  |  |  |  |  |  |  |  |  |  |  |  |  |  |  |  |  |  |  |  | CTS |  |  |  |  |  |  |  |  |  |  |  |  |  |  |  |  |  |  |  |  |  | PD11 | PD11 | BUTTON4 | 11
59 |  | PD12 |  |  |  |  |  |  |  |  |  |  |  | CH1 |  |  |  |  |  |  |  |  | RTS |  |  |  |  |  |  |  |  |  |  |  |  |  |  |  |  |  |  |  |  |  | PD12 | TIM4_CH1 | ENC1A
60 |  | PD13 |  |  |  |  |  |  |  |  |  |  |  | CH2 |  |  |  |  |  |  |  |  |  |  |  |  |  |  |  |  |  |  |  |  |  |  |  |  |  |  |  |  |  |  | PD13 | TIM4_CH2 | ENC1B | 13
61 |  | PD14 |  |  |  |  |  |  |  |  |  |  |  | CH3 |  |  |  |  |  |  |  |  |  |  |  |  |  |  |  |  |  |  |  |  |  |  |  |  |  |  |  |  |  |  | PD14 | PD14 | BUTTON_ON | 14
62 |  | PD15 |  |  |  |  |  |  |  |  |  |  |  | CH4 |  |  |  |  |  |  |  |  |  |  |  |  |  |  |  |  |  |  |  |  |  |  |  |  |  |  |  |  |  |  | PD15 | PD15 | IMU_INT
63 |  | PC6 |  |  |  |  |  |  |  |  |  | CH1 |  |  |  | CH1 |  |  |  |  |  |  |  |  |  |  |  |  |  |  |  |  |  |  |  |  |  | D6 |  |  |  |  |  |  | PC6 | TIM8_CH1 | SERVO1
64 |  | PC7 |  |  |  |  |  |  |  |  |  | CH2 |  |  |  | CH2 |  |  |  |  |  |  |  |  |  |  |  |  |  |  |  |  |  |  |  |  |  | D7 |  |  |  |  |  |  | PC7 | TIM8_CH2 | SERVO2
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

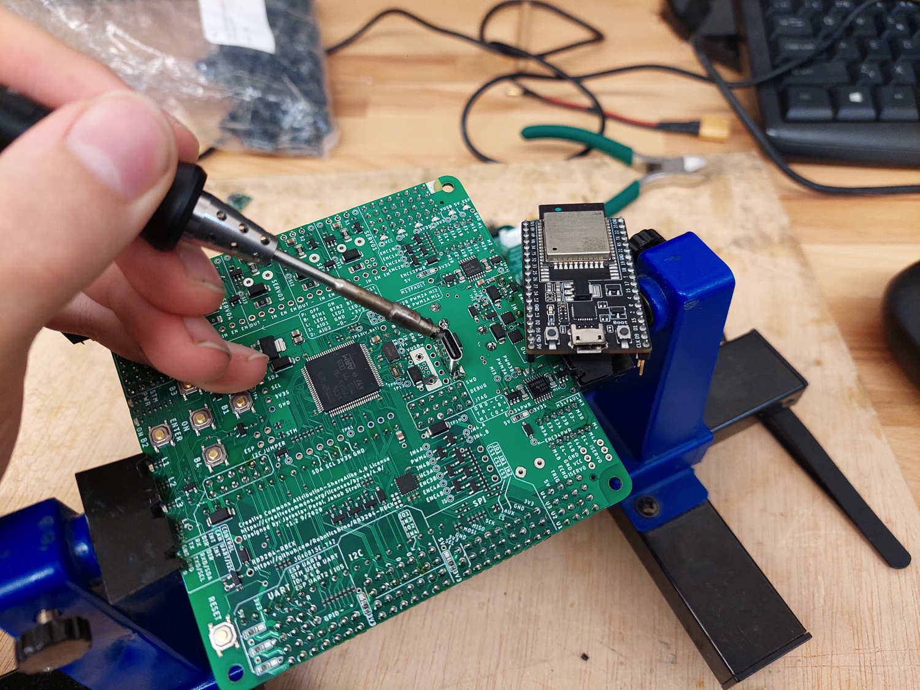
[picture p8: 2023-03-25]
docs/media/rbcx-demo.png

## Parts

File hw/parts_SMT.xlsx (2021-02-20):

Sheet: Import from Eagle BOM
Description | Qty | Device | ID | Value | MF_ID | MF | LCSC_ID | Package | PADS | EXTENDED | PRICE_1PLUS | PRICE_10PLUS | PRICE_30PLUS | PRICE_50PLUS | PRICE_100PLUS | PRICE_200PLUS | PRICE_500PLUS | PRICE_1000PLUS | PRICE_2000PLUS | PRICE_DATE | VOLTAGE | DIELECTRIC | DESCRIPTION | SUMA | Pcs for 50 PCB | Price if 50 PCB | Price if 1 PCB | Minus
Mainstream Performance line, ARM Cortex-M3 MCU with 512 Kbytes Flash, 72 MHz CPU, motor control, USB and CAN | 1 | STM32F103VCT6 | IC13 | STM32F103VCT6 | STM32F103VCT6 | STMicroelectronics | C8313 | LQFP-100_14.0x14.0x0.5P | 100 | NO | $2.4287 | $2.4287 | $2.0653 | $2.0653 | $2.0653 | $2.0653 | $2.0653 | $2.0653 | $2.0653 | 2020-03-27 |  |  | High-density performance line ARM-based 32-bit MCU with 256 KB Flash, USB, CAN, 8 timers, 3 ADCs, 13 communication interfaces | $2.58 | 50 | $2.07 | $2.58
MPU-6050 Six-Axis (Gyro + Accelerometer) MEMS MotionTracking™ Devices | 1 | MPU-6050 | IC12 | MPU-6050 | MPU-6050 | TDK InvenSense | C24112 | QFN-24_EP_4.0x4.0x0.5P | 24 | NO | $2.1715 |  | $1.8096 |  |  |  |  |  |  | 2020-05-09 |  |  | ATTITUDE SENSORS QFN-24_4X4X05P ROHS | $2.21 | 50 | $0.00 | $2.21 | $2.21
 | 2 | DRV8833PWP | IC2, IC5 | DRV8833PWP | DRV8833PWPR | Texas Instruments | C50506 | HTSSOP-16_EP_4.4x5.0x0.65P | 16 | YES | $0.5155 |  | $0.3747 |  |  |  |  |  |  | 2020-03-27 |  |  | Dual Motor driver 10V 1.5A | $1.08 | 100 | $0.00 | $1.08
 | 2 | P-MOSFET-MLP_HS | Q1, Q2 | AON7421 | AON7421 | Alpha & Omega Semicon | C115842 | DFN3.3X3.3 EP | 8 | YES | $0.4798 | $0,3537 | $0,3290 |  | $0,3058 |  |  |  |  | 2020-05-09 |  |  | P MOSFET 19V 35A 7mΩ | $0.98 | 100 | $0,3058 | $0.98
 | 8 | INA180A | IC3, IC4, IC6, IC7, IC8, IC9, IC10, IC11 |  | INA180A4IDBVT | Texas Instruments | C133969 | SOT-23-5L | 5 | YES | $0.3943 | $0.2986 | $0.2812 |  | $0.2638 |  | $0.2566 | $0.2522 | $0.2493 | 2020-03-27 |  |  | PMIC - CURRENT & POWER MONITORS & REGULATORS 1 200 V/V Â±0.1% 105KHZ -0.2V ~ 26V 2.7V ~ 5.5V SOT-23-5 ROHS | $3.21 | 400 | $0.00 | $3.21 | $3.21
SMD Crystal 8 Mhz-20pF-10ppm-80R; | 1 | 5032/2P | Y1 | 8MHz | X50328MSB2GI | Yangxing Tech | C115962 | SMD-5032_2P | 2 | NO | $0.1707 |  |  | $0.1106 |  |  |  |  |  | 2020-03-27 |  |  | SMD Crystal 8 MHz-20pF-10ppm-80R; | $0.17 | 50 | $0.11 | $0.17
SMD Crystal 32.768 Khz-12.5pF-20ppm | 1 | 3215_2P | Y2 | 32.768Hz | Q13FC1350000400 | Seiko Epson | C32346 | SMD-3215_2P | 2 | NO | $0.1542 |  |  | $0.0973 |  |  |  |  |  | 2020-03-27 |  |  | SMD Crystal 32.768 kHz-12.5pF-20ppm | $0.16 | 50 | $0.10 | $0.16
VOLTAGE REGULATOR | 1 | AMS1117 | IC1 | AMS1117-3.3 | AMS1117-3.3 | Advanced Monolithic Systems | C6186 | SOT-223 | 4 | NO | $0.1230 |  |  |  | $0.0750 |  |  |  |  | 2020-03-27 | 3.3 |  | LOW DROPOUT REGULATOR(LDO) 3V3 1A SOT-223 ROHS | $0.13 | 50 | $0.00 | $0.13
RESISTOR, European symbol | 8 | R-EU_R1206 | R124, R125, R133, R134, R140, R142, R144, R146 | 5m | MRMF3216(1206)LR005FTN | SUP | C76290 | R1206 | 2 | YES | $0.0794 |  |  |  | $0.0453 |  |  |  |  | 2020-03-27 |  |  | CURRENT SENCE CHIP RESISTOR ±1% 1W | $0.66 | 400 | $0.00 | $0.66 | $0.66
LED | 2 | LEDCHIPLED_0603 | LED13, LED14 | green | 19-217/GHC-YR1S2/3T | Everlight Elec | C72043 | LED_0603 | 2 | NO | $0.0407 |  |  |  | $0.0218 |  |  |  |  | 2020-03-27 |  |  | LIGHT EMITTING DIODES (LED) GREEN 520~535NM 112~258MCD@20MA TOP VIEW 0603 ROHS | $0.09 | 100 | $0.02 | $0.09
 | 4 | SHOTTKY-SOD123 | D7, D9, D10, D15 | B5819W | B5819W | Foshan Blue Rocket Elec | C8598 | SOD-123 | 2 | NO | $0.0342 |  |  |  | $0.0176 |  |  |  |  | 2020-03-17 |  |  | 40V 1A 600mV @ 1A SOD-123 Schottky Barrier Diodes (SBD) RoHS | $0.15 | 200 | $0.00 | $0.15
Silicon Schottky Diodes | 13 | BAS40-04 | D11, D12, D13, D14, D17, D18, D19, D20, D26, D27, D28, D29, D30 | BAS40-04 | BAS40-04LT1G | ON Semicon | C78265 | SOT-23-3 | 3 | YES | $0.0338 |  |  |  | $0.0174 |  |  |  |  | 2020-03-27 |  |  | 40V 120mA 1000mV @ 40mA SOT-23 Dual Schottky Barrier Diodes (SBD) common cathode/anode RoHS | $0.50 | 650 | $0.00 | $0.50
 | 12 | SHOTTKY-SMA | D1, D2, D3, D4, D5, D6, D8, D22, D23, D24, D25, D31 | SS34 | SS34 | MDD)icrodiode Electronics) | C8678 | SMA,DO-214AC | 2 | NO | $0.0335 |  |  |  | $0.0173 |  |  |  |  | 2020-03-27 |  |  | 40V 3A 400mV @ 1A 550mV @ 3A DO-214AC Schottky Barrier Diodes (SBD) RoHS | $0.44 | 600 | $0.00 | $0.44
Silicon Schottky Diodes | 2 | BAS40-05 | D16, D21 | BAS40-05 | BAS40-05 | Changjiang Electronics Tech (CJ) | C10040 | SOT-23-3 | 3 | YES | $0.0293 |  |  |  |  | $0.0145 |  |  |  | 2020-03-27 |  |  | 40V 200mA 1000mV @ 40mA SOT-23 Dual Schottky Barrier Diodes (SBD) common cathode RoHS | $0.07 | 100 | $0.00 | $0.07
LED | 2 | LEDCHIPLED_0603 | LED19, LED20 | blue | 19-217/BHC-ZL1M2RY/3T | Everlight Elec | C72041 | LED_0603 | 2 | NO | $0.0267 |  |  |  |  | $0.0133 |  |  |  | 2020-03-27 |  |  | LIGHT EMITTING DIODES (LED) BLUE 465~475NM 11.5~28.5MCD@5MA TOP VIEW 0603 ROHS | $0.06 | 100 | $0.00 | $0.06
LED | 2 | LEDCHIPLED_0603 | LED15, LED16 | yellow | 19-213/Y2C-CQ2R2L/3T(CY) | Everlight Elec | C72038 | LED_0603 | 2 | NO | $0.0262 |  |  |  |  | $0.0130 |  |  |  | 2020-03-27 |  |  | LIGHT EMITTING DIODES (LED) YELLOW 585.5~591.5NM 90~180MCD@20MA TOP VIEW 0603 ROHS | $0.06 | 100 | $0.00 | $0.06
CAPACITOR, European symbol | 13 | C-EUC0805 | C3, C4, C5, C6, C14, C19, C36, C37, C38, C39, C41, C51, C53 | 10uF 25 V | CL21A106KAYNNNE | Samsung Electro-Mechanics | C15850 | C0805 | 2 | NO | $0.0221 |  |  |  |  | $0.0106 |  |  |  | 2020-03-27 | 25 | X5R | MULTILAYER CERAMIC CAPACITOR | $0.33 | 650 | $0.00 | $0.33
 | 8 | N-MOSFET-SOT23-GSD | Q3, Q4, Q5, Q6, Q7, Q8, Q9, Q10 | 2N7002 | 2N7002 | Changjiang Electronics Tech (CJ) | C8545 | SOT-23-3 | 3 | NO | $0.0218 |  |  |  |  | $0.0104 |  |  |  | 2020-03-28 |  |  | N MOSFET 60V 115mA 7Ω | $0.21 | 400 | $0.01 | $0.21
CAPACITOR, European symbol | 3 | C-EUC0603 | C8, C16, C21 | 2.2uF 16 V | CL10A225KO8NNNC | Samsung Electro-Mechanics | C23630 | C0603 | 2 | NO | $0.0103 |  |  |  |  | $0.0044 |  |  |  | 2020-03-27 | 16 | X5R | MULTILAYER CERAMIC CAPACITOR | $0.04 | 150 | $0.00 | $0.04
CAPACITOR, European symbol | 3 | C-EUC0402 | C15, C20, C42 | 10nF 50 V | CL05B103KB5NNNC | Samsung Electro-Mechanics | C15195 | C0402 | 2 | NO | $0.0083 |  |  |  |  | $0.0033 |  |  |  | 2020-03-27 | 50 | X7R | MULTILAYER CERAMIC CAPACITOR | $0.03 | 150 | $0.00 | $0.03
RESISTOR, European symbol | 5 | R-EU_R1206 | R68, R135, R136, R137, R138 | 0R | 1206W4F0000T5E | Uniroyal Elec | C17888 | R1206 | 2 | NO | $0.0082 |  |  |  |  | $0.0032 |  |  |  | 2020-03-27 |  |  | CHIP RESISTOR 0R - JUMPER (MAX 2A, 10 A peak) | $0.06 | 250 | $0.0032 | $0.06
LED | 18 | LEDCHIPLED_0603 | LED1, LED2, LED3, LED4, LED5, LED6, LED7, LED8, LED9, LED10, LED11, LED12, LED17, LED18, LED21, LED22, LED23, LED24 | red | KT-0603R | Hubei KENTO Elec | C2286 | LED_0603 | 2 | NO | $0.0079 |  |  |  |  | $0.0031 |  |  |  | 2020-03-27 |  |  | LIGHT EMITTING DIODES (LED) RED 520~625NM 90~100MCD@20MA TOP VIEW 0603 ROHS | $0.20 | 900 | $0.00 | $0.20
CAPACITOR, European symbol | 10 | C-EUC0402 | C7, C9, C10, C11, C12, C13, C32, C33, C34, C35 | 1uF 25 V | CL05A105KA5NQNC | Samsung Electro-Mechanics | C52923 | C0402 | 2 | NO | $0.0078 |  |  |  |  | $0.0031 |  |  |  | 2020-03-27 | 25 | X5R | MULTILAYER CERAMIC CAPACITOR | $0.11 | 500 | $0.00 | $0.11
CAPACITOR, European symbol | 16 | C-EUC0402 | C17, C18, C22, C23, C28, C29, C30, C31, C43, C44, C46, C47, C48, C49, C50, C52 | 100nF 16 V | CL05B104KO5NNNC | Samsung Electro-Mechanics | C1525 | C0402 | 2 | NO | $0.0043 |  |  |  |  | $0.0016 |  |  |  | 2020-03-27 | 16 | X7R | MULTILAYER CERAMIC CAPACITOR | $0.12 | 800 | $0.00 | $0.12
CAPACITOR, European symbol | 2 | C-EUC0402 | C54, C56 | 18pF 50V | 0402CG180J500NT | Guangdong Fenghua Advanced Tech | C1549 | C0402 | 2 | NO | $0.0019 |  |  |  |  | $0.0006 |  |  |  | 2020-03-27 | 50 | C0G | MULTILAYER CERAMIC CAPACITOR | $0.01 | 100 | $0.00 | $0.01
RESISTOR, European symbol | 6 | R-EU_R0402 | R1, R55, R62, R79, R80, R114 | 100k | 0402WGF1003TCE | Uniroyal Elec | C25741 | R0402 | 2 | NO | $0.0019 |  |  |  |  |  |  | $0.0006 |  | 2020-03-27 |  |  | CHIP RESISTOR ±1% 1/16W | $0.03 | 300 | $0.00 | $0.03
CAPACITOR, European symbol | 1 | C-EUC0402 | C45 | 2n2 | 0402B222K500NT | Guangdong Fenghua Advanced Tech | C1531 | C0402 | 2 | NO | $0.0018 |  |  |  |  |  |  | $0,0006 |  | 2020-05-09 | 16V |  | MULTILAYER CERAMIC CAPACITORS MLCC - SMD/SMT 2.2NF 50V 0402 ROHS | $0.0048 | 50 | $0.00 | $0.0048
CAPACITOR, European symbol | 2 | C-EUC0402 | C55, C57 | 6.8pF 50 V | 0402CG6R8C500NT | Guangdong Fenghua Advanced Tech | C1576 | C0402 | 2 | NO | $0.0018 |  |  |  |  | $0.0006 |  |  |  | 2020-03-27 | 50 | C0G | MULTILAYER CERAMIC CAPACITOR | $0.01 | 100 | $0.00 | $0.01
RESISTOR, European symbol | 7 | R-EU_R0603 | R24, R25, R26, R47, R58, R119, R126 | 0R | 0603WAF0000T5E | Uniroyal Elec | C21189 | R0603 | 2 | NO | $0.0016 |  |  |  |  |  |  | $0,0005 |  | 2020-05-09 |  |  | CHIP RESISTOR - SURFACE MOUNT 0OHMS ±1% 1/10W 0603 ROHS | $0.03 | 350 | $0.00 | $0.03
RESISTOR, European symbol | 2 | R-EU_R0402 | R3, R8 | 24k | 0402WGF2402TCE | Uniroyal Elec | C25769 | R0402 | 2 | NO | $0.0011 |  |  |  |  |  |  | $0.0004 |  | 2020-03-27 |  |  | CHIP RESISTOR ±1% 1/16W | $0.01 | 100 | $0.00 | $0.01
RESISTOR, European symbol | 2 | R-EU_R0402 | R9, R75 | 5k6 | 0402WGF5601TCE | Uniroyal Elec | C25908 | R0402 | 2 | NO | $0.0011 |  |  |  |  |  |  | $0.0004 |  | 2020-03-27 |  |  | CHIP RESISTOR ±1% 1/16W | $0.01 | 100 | $0.00 | $0.01
RESISTOR, European symbol | 17 | R-EU_R0402 | R12, R13, R27, R28, R40, R41, R45, R46, R54, R67, R69, R83, R84, R115, R116, R161, R162 | 4k7 | 0402WGF4701TCE | Uniroyal Elec | C25900 | R0402 | 2 | NO | $0.0009 |  |  |  |  |  |  | $0.0003 |  | 2020-03-27 |  |  | CHIP RESISTOR ±1% 1/16W | $0.07 | 850 | $0.00 | $0.07
RESISTOR, European symbol | 19 | R-EU_R0402 | R14, R15,R20, R21, R22, R23, R120, R121, R122, R123, R127, R128, R129, R130, R147, R148, R149, R150, R151 | 2k2 | 0402WGF2201TCE | Uniroyal Elec | C25879 | R0402 | 2 | NO | $0.0009 |  |  |  |  |  |  | $0.0003 |  | 2020-03-27 |  |  | CHIP RESISTOR ±1% 1/16W | $0.07 | 950 | $0.00 | $0.07
RESISTOR, European symbol | 12 | R-EU_R0402 | R16, R17, R18, R19, R81, R82, R117, R118, R139, R141, R143, R145 | 1k | 0402WGF1001TCE | Uniroyal Elec | C11702 | R0402 | 2 | NO | $0.0009 |  |  |  |  |  |  | $0.0003 |  | 2020-03-27 |  |  | CHIP RESISTOR ±1% 1/16W | $0.05 | 600 | $0.00 | $0.05
RESISTOR, European symbol | 8 | R-EU_R0402 | R2, R4, R6, R10, R11, R76, R131, R132 | 10k | 0402WGF1002TCE | Uniroyal Elec | C25744 | R0402 | 2 | NO | $0.0009 |  |  |  |  |  |  | $0.0003 |  | 2020-03-27 |  |  | CHIP RESISTOR ±1% 1/16W | $0.03 | 400 | $0.00 | $0.03
RESISTOR, European symbol | 76 | R-EU_R0402 | R5, R29, R30, R31, R32, R33, R34, R35, R36, R37, R38, R39, R42, R43, R44, R48, R49, R50, R51, R52, R53, R56, R57, R59, R60, R61, R63, R64, R65, R66, R70, R71, R73, R74, R77, R78, R85, R86, R87, R88, R89, R90, R91, R92, R93, R94, R95, R96, R97, R98, R99, R100, R101, R102, R103, R104, R105, R106, R107, R108, R109, R110, R111, R112, R113, R152, R153, R154, R155, R156, R157, R158, R159, R160, R163, R164 | 330R | 0402WGF3300TCE | Uniroyal Elec | C25104 | R0402 | 2 | NO | $0.0009 |  |  |  |  |  |  | $0.0003 |  | 2020-03-27 |  |  | CHIP RESISTOR ±1% 1/16W | $0.30 | 3800 | $0.00 | $0.30
RESISTOR, European symbol | 1 | R-EU_R0402 | R7 | 1M | 0402WGF1004TCE | Uniroyal Elec | C26083 | R0402 | 2 | NO | $0.0009 |  |  |  |  |  |  | $0.0003 |  | 2020-03-27 |  |  | CHIP RESISTOR ±1% 1/16W | $0.0039 | 50 | $0.00 | $0.0039
RESISTOR, European symbol | 1 | R-EU_R0402 | R72 | 1k5 | 0402WGF1501TCE | Uniroyal Elec | C25867 | R0403 | 2 | NO | $0.0009 |  |  |  |  |  |  | $0.0003 |  | 2020-04-20 |  |  | CHIP RESISTOR ±1% 1/16W | $0.0039 | 50 | $0.00 | $0.0039
 |  |  |  |  |  |  |  |  |  |  |  |  |  |  |  |  |  |  |  |  |  |  |  | $14.25 |  | $2.31 | $71.26 | 6.0811

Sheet: Export for JLCPCB
Qty | Designator | Footprint | Comment | LCSC Part # (optional) | Description (optional)
7 | R24, R25, R26, R47, R58, R119, R126 | R0603 | 0R | C21189 | 0603WAF0000T5E
5 | R68, R135, R136, R137, R138 | R1206 | 0R | C17888 | 1206W4F0000T5E
6 | R1, R55, R62, R79, R80, R114 | R0402 | 100k | C25741 | 0402WGF1003TCE
16 | C17, C18, C22, C23, C28, C29, C30, C31, C43, C44, C46, C47, C48, C49, C50, C52 | C0402 | 100nF 16 V | C1525 | CL05B104KO5NNNC
8 | R2, R4, R6, R10, R11, R76, R131, R132 | R0402 | 10k | C25744 | 0402WGF1002TCE
3 | C15, C20, C42 | C0402 | 10nF 50 V | C15195 | CL05B103KB5NNNC
13 | C3, C4, C5, C6, C14, C19, C36, C37, C38, C39, C41, C51, C53 | C0805 | 10uF 25 V | C15850 | CL21A106KAYNNNE
2 | C54, C56 | C0402 | 18pF 50V | C1549 | 0402CG180J500NT
12 | R16, R17, R18, R19, R81, R82, R117, R118, R139, R141, R143, R145 | R0402 | 1k | C11702 | 0402WGF1001TCE
1 | R72 | R0402 | 1k5 | C25867 | 0402WGF1501TCE
1 | R7 | R0402 | 1M | C26083 | 0402WGF1004TCE
10 | C7, C9, C10, C11, C12, C13, C32, C33, C34, C35 | C0402 | 1uF 25 V | C52923 | CL05A105KA5NQNC
2 | R3, R8 | R0402 | 24k | C25769 | 0402WGF2402TCE
19 | R14, R15, R20, R21, R22, R23, R120, R121, R122, R123, R127, R128, R129, R130, R147, R148, R149, R150, R151 | R0402 | 2k2 | C25879 | 0402WGF2201TCE
1 | C45 | C0402 | 2n2 | C1531 | 0402B222K500NT
8 | Q3, Q4, Q5, Q6, Q7, Q8, Q9, Q10 | SOT-23-3 | 2N7002 | C8545 | 2N7002
3 | C8, C16, C21 | C0603 | 2.2uF 16 V | C23630 | CL10A225KO8NNNC
1 | Y2 | SMD-3215_2P | 32.768Hz | C32346 | Q13FC1350000400
76 | R5, R29, R30, R31, R32, R33, R34, R35, R36, R37, R38, R39, R42, R43, R44, R48, R49, R50, R51, R52, R53, R56, R57, R59, R60, R61, R63, R64, R65, R66, R70, R71, R73, R74, R77, R78, R85, R86, R87, R88, R89, R90, R91, R92, R93, R94, R95, R96, R97, R98, R99, R100, R101, R102, R103, R104, R105, R106, R107, R108, R109, R110, R111, R112, R113, R152, R153, R154, R155, R156, R157, R158, R159, R160, R163, R164 | R0402 | 330R | C25104 | 0402WGF3300TCE
17 | R12, R13, R27, R28, R40, R41, R45, R46, R54, R67, R69, R83, R84, R115, R116, R161, R162 | R0402 | 4k7 | C25900 | 0402WGF4701TCE
1 | Y1 | SMD-5032_2P | 8MHz | C115962 | X50328MSB2GI
2 | R9, R75 | R0402 | 5k6 | C25908 | 0402WGF5601TCE
8 | R124, R125, R133, R134, R140, R142, R144, R146 | R1206 | 5m | C76290 | MRMF3216(1206)LR005FTN
2 | C55, C57 | C0402 | 6.8pF 50 V | C1576 | 0402CG6R8C500NT
1 | IC1 | SOT-223 | AMS1117-3.3 | C6186 | AMS1117-3.3
4 | D7, D9, D10, D15 | SOD-123 | B5819W | C8598 | B5819W
13 | D11, D12, D13, D14, D17, D18, D19, D20, D26, D27, D28, D29, D30 | SOT-23-3 | BAS40-04 | C78265 | BAS40-04LT1G
2 | D16, D21 | SOT-23-3 | BAS40-05 | C10040 | BAS40-05
2 | LED19, LED20 | LED_0603 | blue | C72041 | 19-217/BHC-ZL1M2RY/3T
2 | IC2, IC5 | HTSSOP-16_EP_4.4x5.0x0.65P | DRV8833PWP | C50506 | DRV8833PWPR
2 | LED13, LED14 | LED_0603 | green | C72043 | 19-217/GHC-YR1S2/3T
8 | IC3, IC4, IC6, IC7, IC8, IC9, IC10, IC11 | SOT-23-5L | INA180A4 | C133969 | INA180A4IDBVT
1 | IC12 | QFN-24_EP_4.0x4.0x0.5P | MPU-6050 | C24112 | MPU-6050
2 | Q1, Q2 | DFN3.3X3.3 EP | AON7421 | C115842 | AON7421
18 | LED1, LED2, LED3, LED4, LED5, LED6, LED7, LED8, LED9, LED10, LED11, LED12, LED17, LED18, LED21, LED22, LED23, LED24 | LED_0603 | red | C2286 | KT-0603R
12 | D1, D2, D3, D4, D5, D6, D8, D22, D23, D24, D25, D31 | SMA,DO-214AC | SS34 | C8678 | SS34
1 | IC13 | LQFP-100_14.0x14.0x0.5P | STM32F103VCT6 | C8313 | STM32F103VCT6
2 | LED15, LED16 | LED_0603 | yellow | C72038 | 19-213/Y2C-CQ2R2L/3T(CY)

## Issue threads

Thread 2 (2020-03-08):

[CZ] MainBoarsSCH - dodělat/zkontrolovat

JarekParal, 2020-03-08:
## Dodělat

### Sheet Power
- [x] vybrat výkonové tranzistory a signálové tranzistory
- [x] doplnit atributy u tlačítek a ověřit dostupnost na JLCPCB

### Sheet Motors
- [x] @cednik dodat LCSC_ID pro BAS40-05, SS34, @JarekParal doplní atributy

## Zkontrolovat
- [x] OZ INA180A4 - ověřit správnou velikost pouzdra - ve schema je SC-70-5 a v [datasheetu/JLCPBC SOT-23-5](https://datasheet.lcsc.com/szlcsc/1811211019_Texas-Instruments-TI-INA180A4IDBVT_C133969.pdf) což [jsou zdá se různá pouzdra](https://en.wikipedia.org/wiki/Small-outline_transistor#SOT23-5.2C_SOT353)

## Otázky
- [x] jak byla vytvořena značka `+3V3 STM`?
- [x] proč byli odebrány tlačítka v listu `Coprocessor`

## Podměty

### Atributy
- dolňujme atributy u součástek, hned jak součástku vybereme a začnemé dávat do schema (ideálně vyplnit u první součástky a pak už jen rozkopírovat) - platí i u odporů, kondenzátorů atd. => ušetří nám to pak hromadu času v budoucnu
- doplňované atributy: Description, Manufacturer (MF), MF_ID, LCSC_ID, Package, Price (PRICE_1PLUS, PRICE_30PLUS, PRICE_100PLUS...), Extended_part (Yes/No), Number of pads (PADS)

cednik, 2020-03-08:
- INA180A4: máš pravdu, pouzdro opravím
- `+3V3 SMT`: knihovna supply - jsou v ní všechny použité symboly napájení. Celkem bude na desce 5 různých "globálních" napájení (nepočítám napájení pro serva, které je ve schématu u sebe, a podobné): beteriové napětí `VCC`, `+3V3S` a `+5V0S` napájení pro STM, které musí fungovat nezávisle na ESP32 (pokud toto na desce zrovna nebude osazené) a `+3V3` s `+5V` napájecí napětí pro ESP32 a věci k němu připojené. `GND` je pro všechno společné. Bez zvláštních symbolů by v tom byl hrozný zmatek.
- Odebrání tlačítek: ten symbol byl příšerný. Nakreslil jsem hezčí. Zatím je použit v listu napájení. Do zbytku doplním, jakmile se k daným listům dostanu.
- Atributy u odporů a kondenzátorů zatím nejsou záměrně. Aktuálně jsou u součástek napsané jejich optimální hodnoty z pohledu elektrického (aspoň dle mého názoru :-) ). Až bude schéma kompletní, je potřeba ho znovu projít a udělat optimalizaci kvůli ceně a množství použitých hodnot. Pak má smysl doplňovat atributy, nejlépe nějakým skriptem :-)

JarekParal, 2020-04-12:
Udělal jsem si menší rešerši na velikost DPS, počet vrstev a případné cesty jak ušetřit místo.

## Velikost DPS a počet vrstev versus cena

yaqwsx, 2020-04-12:
Když se dívám na schéma, podle mě bez 4 vrstev nemáme šanci anebo u toho minimálně přijdeme o vlasy. O co přeplatíme na prototypech, o to rychleji (a lépe) to budeme mít hotové. Cena při výrobě 50 ks je v kontextu tábora zanedbatelná (rozdíl cca 1 USD). Rozdíl při objednání dalších desek (10 ks) - 0.5 vs 3 USD, mi přijde také akceptovatelný. Toť můj názor a počet vrstev.

Co se týká rozměru - já vždy preferuji co nejmenší desky, ale to je asi má osobní úchylka.

Ad svorkovnice: a) se mi nelíbí, b) c) jsou za mě ok.

dzarda, 2020-04-12:
Zaroutovat to určitě půjde, jde ale o komfort (vlasy) a rychlost, což nás momentálně trápí nejvíc.  Když jsme dělali RBC, bránil jsem se stejně. Nakonec to šlo, ale byl to "Sokoban". Ta cena 4 vrstev je pořád za hubičku, i pro 12x10.

PS nemá myslím smysl tahat GND cesty, to bývá nejlepší vyřešit polygonem - jen je u toho potřeba uvažovat o reálných tocích proudu.

JarekParal, 2020-04-14:
@dzarda Na RBC byl rozdíl v tom, že u driverů jsi prakticky měl 4 vrstvy, protože byla na samostatné DPS. Zároveň tady je kolem driverů mnohem víc součástek kvůli měření proudu.
Ale možná už jsem vymyslel, jak by se to dalo zaroutovat i na 2 vrstvách, když se upraví dispozice motorových svorkovnic.

cednik, 2020-04-14:
Když koukám na Jarkem zaroutované napájení, pojďme do čtyř vrstev. Cenový rozdíl není tak velký - naše vlasy jsou dražší.
Honzovu úchylku na minimální rozměry desky sdílím.

### Svorkovnice

- Je to sice hezká feature, ale jejich úplnému zrušení bych se kupodivu nebránil. Pokud se povede udělat destičku s enkodérem, která se na motor jen připlácne a kontakty motoru se zapájí přímo do ní, pak budeme motory stejně připojovat jedním šestižilovým kabelem.
- Varienta **b** se mi nelíbí. Za prvé si nemyslím, že to moc pomůže, za druhé narazíme na proudové limity - jak u svorkovnice, tak u připojovaných drátů (ten nejtlustší drát, co jde strčit do @JarekParal návrhu č. 1 sice zvládne 10 A, ale ohřeje se přitom o 40 °C [[wiki:awg](https://en.wikipedia.org/wiki/American_wire_gauge#Tables_of_AWG_wire_sizes)]).
- S variantou **c** bych se smířil. Pár milimetrů místa ušetří, drivery půjdou posunout víc ke kraji desky a budou víc zarovnané se zapínáním uprostřed s velkými svorkovnicemi.

Ovšem nelíbí se mi šroubovací svorkovnice v rozteči 2.54 mm - potřebuješ na ně hodně malý šroubovák, což bývá často problém. Jen nevím, jestli ty navrhované pružinkové dvoudírové ušetří nějaké místo v tom správném směru (šířka/hloubka té svorkovnice). Místo, ušetřené její délkou, mně moc nenapadá, jak využít.

P.S.: @dzarda tahání GND cest = uvažování o reálných tocích proudu. Ten polygon tam pak stejně bude, ale budeš si jistý, že proud má dost místa k tečení a nepřehlédls někde propojení jen nějakým chlupem.

JarekParal, 2020-04-28:
Svorkovnice pro motory byli z návrhu odebrány kvůli nedostatku místa na DPS.

Pinheady pro enkodéry (a motory) jsou nahrazeny [JST PH 2.0 mm konektory](https://www.aliexpress.com/item/32810190369.html), jelikož tyto konektory používají i [čínské motory s enkodéry](https://www.aliexpress.com/item/32944478481.html), dají se k nim koupit [snad kvalitní nakrymplované kabely](https://www.aliexpress.com/item/32890983007.html), které nejdou otočit.

RBCX bude navrhována jako 4 vrstvá DPS, protože ve dvou vrstvách se nelze vymotat. Ale cílem je zachovat rozměry 10x10 cm.

dzarda, 2020-05-03:
Přemýšlel jsem nad option jumperama - nechcem radši nahradit za 0R součástky s defaultním výběrem jedné varianty, ať odpadne manuální postprocessing?

yaqwsx, 2020-05-04:
Varianta nechat si tam u JLC osadit rezistor se mi hodně líbí. Zvládneme udělat footprint tak, že zůstane zachovaný současný tvar pájecích plošek a JLC nám do něj korektně umístí 0R odpor (@cednik @JarekParal)? Proč to chci:
- získáme defaultní konfiguraci z výroby (juch)
- když to chci změnit, přejedu to pájkou, setřu odpor, a stále mám věc, která se pohodlně pájí, protože je velká. Kdybych tam měl pady přímo pro 2 rezistory, tak ta změna bude fakt bolet.

JarekParal, 2020-05-04:
Včera jsme @dzarda návrh řešili a taky se nám líbí. Je tam jeden zádrhel.

Pokud chceme nulové výkonové odpory

cednik, 2020-05-04:
Defaultní konfigurace je super nápad. Včera jsme se o tom bavili s @JarekParal po Skypu.
Asi by neměl být problém nechat na stávající footprint osadit 0R 0603, akorát budu muset trochu překopat tu součástku, abych to do osazovacích dat nemusel dopisovat ručně.
Momentálně mám nastavovací jumpery ze spodní strany desky, aby byly přístupné ze stejné strany, jako konektory. Kvůli defaultnímu osazení bych je musel hodit nahoru a pak se k nim v robotovi nepůjde dostat bez odšroubování desky, ale to asi není tolik na škodu.

Jaké chceme defaultní hodnoty (návrhy):

- **SPI**: dvě jsou pevně 3V3, jedno nastavitelné (ale pouze napájení, na signálech level shifter není) @yaqwsx jaké napájení chce tvoje senzorická lišta?
- **I2C**: dvě 3V3, dvě nastavitelné (včetně level shiftrů) - navrhuji **5V**
- **UART**: **3V3**
- **UART2**: (JP40, stejný pinout jakou UART, co si tam uživatel v ESP naprogramuje je na něm - 2. UART/I2C/CAN/cokoli) **3V3**
- **UART koproc**: (JP33) **5V** - STM má 5V tolerantní piny
- **enkodéry**: **3V3** - podle vybraných hallových sond
- **konektor komunikačního UARTu mezi STM a ESP**: (JP54, dětem se stejně nebude osazovat) - **neosazovat**
- **SWO signál na SDW konektoru STM**: možnosti jsou debug UART TX / SWO pin. SWO pin je bohužel sdílený se signálem jednoho enkodéru. Jde prakticky jen o pohodlnost, debug UART je vyveden na samostatném konektoru.

Schéma konektorů:
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

yaqwsx, 2020-05-04:
Lišta by měla fungovat jak na 3V3, tak na 5V (je třeba jen správně osadit rezistory pro LEDky). Čip je 2.7-5V: http://ww1.microchip.com/downloads/en/DeviceDoc/21295d.pdf

JarekParal, 2020-05-19:
Done #15 and 14de8e774d4055421ac026269bed3bde5665a5fa

Closed 2020-05-19.

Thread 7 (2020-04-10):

[RFC] Data multiplex & protocol

dzarda, 2020-04-10:
There are three logical data streams:

- CDC to coprocessor
- CDC to ESP tunnel
- ESP to coprocessor

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

One option is to open two CDC channels, but I think it does more bad than good and only partially solved the problem.

For simplicity sake we probably want to share the protocol on both CDC and downstream UART. Protobuf can be used to describe the whole data domain.

```proto3
message CoprocIn {
  ...
}

message CoprocOut {
  ...
}

message Passthrough {
  bytes content = 0;
}

message Packet {
  oneof type_oneof {
    CoprocIn = 0;
    CoprocOut = 1;
    Passthrough = 2;
  }
}
```

Does this cross OSI layers? Yes. Does it worry me? Not much because this is a very closed system without networking.

@cednik Is this similar to the bangbang-notransaction-architecture you described?

yaqwsx, 2020-04-10:
I like CDC for commands and the second one for ESP32 tunnel. Why should it do more harm than good? It seems like a perfect solution to me - you don't need any special application to encapsulate tunnel communication on the computer side and it works out-of-the-box with all the existing software using a serial line.

When you have two CDCs, I would use only `CoprocIn` and `CoprocOut` without `Packet` - since you don't need it. There's no need to have a common type of messages for both directions of the communication.

Also, I am not sure if I understand the note about OSI layers. We're not building a network device so I see no reason to make it somewhat compatible with OSI.

dzarda, 2020-04-10:
Good points. The OSI thing was OT really sry.

The two CDCs only solve the upstream problem. We have only one physical UART between coproc & ESP. Here we still have to mux the data somehow.

But the pure serial upstream tunnel is a killer feature and I agree with you, we should do it. Could bring just a slight confusion on the PC part - *should I connect to COM4 or COM 6?*

Tasssadar, 2020-04-10:
I'm not sure I understand the way it is supposed to work, but I think I missed one meeting, so I apologize if following is just wrong.

Which UART on ESP32 is coprocesor using, is it the one that is connected to ESP32's USB? Or one of the other ones?

In any case, I don't see the point in tunneling ESP32<->PC. Since the UART is taken up by the coprocesor communication, the app on ESP32 can't use it (unless we somehow implement another "tunneled UART" in our own library, and then the app has to explicitly use that one).

The only reason I see for PC<->ESP32 tunnel is for programming the ESP. In that case, the coprocesor has to recognize that is what is happening and stop communicating via protobufers. Another option is sending the new program to ESP32 via our protobuf protocol and letting it program itself (like OTA), but then you don't need the tunnel at all.

As for the two COM ports, you are able to pass some device/manufacturer strings to the PC: https://github.com/RoboticsBrno/RB3204-RBCX/blob/fw-cdc/fw/rbcx-coprocessor/src/usb_cdc_link.c#L148-L150 If those are per-interface and not per device, they could be used to described each interface. I think that's how we recognize Shupito in Lorris.

BTW, protobufers optimized for MCUs: https://github.com/nanopb/nanopb

yaqwsx, 2020-04-11:
> The two CDCs only solve the upstream problem. We have only one physical UART between coproc & ESP. Here we still have to mux the data somehow.

Ok, I missed that. I thought we have 2 UARTS available.

If we only want to program ESP32 via the bridge, it is easy. Once you detect reboot sequence on the DTR/RTS pins (I hope I got them right), you reset ESP32 and switch to the pure tunnel. Once DTR/RTS returns to normal, you go back to a normal mode.

If we want also redirect the user UART (printf, std::cout & related), it could be done via `funopen` - basically you change the read & write functions for standard input/output. I see several possible drawbacks/open issues here:
- if you connect directly to ESP32 with USB cable you see a binary mess on the terminal
- you cannot transmit boot messages & backtraces in this way since they access UART directly via a function hard-coded in binary blob in drivers supplied by Espressif.
- I am not sure if Arduino uses standard input/output or talks to UART directly

The other option is to just frame our Probuf messages so that chance of confusing them with a regular text stream is negligible. Then the expander consumes all the /rotobufs and unrecognized parts of stream forwards to CDC.

The third option is to use an extra pin between the expander and ESP (not that I hope we have a spare pin @cednik :-P ) and use that to change UART meaning. But I see there a problem when crash happens during sending a protobuf message - we loose the backtrace.

dzarda, 2020-04-11:
I stand corrected, theres:

- a dedicated `ESP_PROG_/UART_` from coproc to ESP32 `TXD0` & `RXD0` presumably for programming (?)
- a shared `EXPANDER-UART-/ from coproc to ESP32 `IO2` & `IO12`, also connected to some pinheaders.

Dunno why I thought there's just one pair.

dzarda, 2020-04-12:
Closing - one UART for verbatim tunneling and second serves as coproc iface

Closed 2020-04-12.

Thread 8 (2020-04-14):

[CZ] USB DP pullup

dzarda, 2020-04-14:
STM32F1 zdá se nemá funkci pullupování DP 1k5 odporem. Co jsem pochopil, tak je to součástí enumerace Full Speed zařízení a dá se pomocí toho udělat "reconnect" - reenumerace, což bychom možná využili při přepnutí na JTAG (nebo možná by se dalo mít víc interfaces zaráz)

Bluepill má ten pullup asi natvrdo na +5V (což je asi blbě, čtu že to má být k 3V - 3V6)

Na našem schéma jsem to nenašel.

libusb tuhle funkci podporuje, dá se tomu port-pin.

cednik, 2020-04-14:
Takže chceš jeden pin STM připojit přes 1k5 na USB DP?
To asi není problém.

dzarda, 2020-05-07:
Už tam je, zavírám

Closed 2020-05-07.

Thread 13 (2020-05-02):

Coproc control communication

dzarda, 2020-05-02:
We decided to dedicate one UART between ESP32 -> STM32 for control communication:
- Asynchronous bidirectional control/state transfers
- Frames containing Protobuf messages

### Link/PHY
Probably some prefix+length as packet start and hope for the best. Do we need some timeout logic for framing?

Gonna start with 115200 since that's the limitation of my dev HW. What about using the *parity bit* as a simple error detection?

### Endpoints
Let's get inspiration from USB. Each request packet should contain some endpoint identification. All endpoints have their ID and type associated with them. This association (in case a status/response message) may be described in protobuf as follows:

```protobuf
message CoprocStatus {
  oneof payload {
    fixed32 protoVersion = 1;
    fixed32 fwVersion = 2;
    float batteryVoltage = 3;
...
    MotorStatus motorAStatus = 32;
    MotorStatus motorBStatus = 33;
...
}

message MotorStatus {
  float current = 1;
  sint32 rotation = 2;
  sint32 velocity = 3;
...
}
```

Ideas welcome

yaqwsx, 2020-05-04:
About link/phy: Since the packets are always received via UART/USB which have strict timing (unlike network), the timeout of several characters/several USB frames is IMHO welcomed. When the user sends an incomplete message, it does not cause the failure of the next one.

I am not sure if I follow the idea from the example. Could you explain it in a different way? Or let's have a call.

To present my view: there are two ways we can go:
- flat commands
- nested/namespaced commands

For the rest of the text, consider we have 2 motors, we want to turn them on/off and we have 2 buttons and we would like to query their status (presses/released).

Flat commands are commands like "turn motor on", "turn motor off", "get status of a button". And they are parametrized by component idx. They are all distinct and simple. Imagine you have a large enum of all possible command types and there is a large dispatcher in the code.

Nested commands are grouped - you have namespace motors (providing command turn on, turn off parametrized by motor idx) and namespace buttons (providing command query parametrized by button idx). Imagine you have 3 enums: namespace, motors commands, button commands.

TLDR: I prefer nested commands.

The obvious advantages for nested commands are:
- there is no huge dispatcher in you code and instead, there are multiple smaller ones that dispatch messages in between each other until one of them performs the command. Which is neat.
- documentation for such protocol is IMHO more readable - you know where to look when you want to control motors
- it is easy to come up with command names
- you can easily add new/remove functionality with local changes in the code.

There are some disadvantages:
- for simple tasks, it adds a little bit of complexity for the user.
- it is unclear what structure should the responses follow (should they also be namespaced?)
- inter-namespace commands do not fit this pattern well, unless (solution at the end of the paragraph). Consider you would like to have a command "When button x is pressed turn motor y" and command "Disable previous functionality". With flat commands this is easy - you introduce two new commands and implement two functions. With nested commands, there is a question - to which namespace it belongs? Motor or button? If we preserve dispatcher isolation, none of them can implement such functionality. Imho, the only solution is to introduce new namespace (with a new dispatcher) - e.g., namespace "chain", which provides command "tie" taking button idx and motor idx.

BTW: Now I am thinking, that dispatcher is a stupid name and maybe we should call it simply a controller.

dzarda, 2020-05-07:
We've got nice results here https://hackmd.io/bpK-FZ-MRfOS4JP8o0kNZg?edit

dzarda, 2020-09-04:
Closing, this is a done deal

Closed 2020-09-04.

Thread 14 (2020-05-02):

Coproc packet framing

dzarda, 2020-05-02:
Dedicate a new UART as a transceiver of packets with a fixed prefix.

Nanopb provides length-prefixed encode/decode, so this doesn't have to be solved here.

Required for #13

yaqwsx, 2020-05-04:
Is there a suitable counterpart of the encoding for desktops? Or do we have to implement it ourselves on the desktop?

Otherwise, I agree with usage of encoding provided by Nanopb.

dzarda, 2020-05-04:
We'll need to make a converter for desktops. I'm thinking like

There's things that implement the COBS encoding like libspf, but I think that's an overkill. PB3 doesn't send zero values, and zero bytes shouldn't appear on the wire unless present in 'bytes' and the like

So I think we may simply use 0x00 as the packet terminator. Together with some timeout, it should be robust enough IMO.

dzarda, 2020-05-04:
> and zero bytes shouldn't appear on the wire

Of course I messed up somewhat - the `fixed` types will contain zeros verbatim

dzarda, 2020-05-14:
More thinking done - I feel like I want the COBS encoding so that zero bytes are only present as packet terminators. Would allow time invariance in receive logic and better robustness imo.

Seems like there's things available OOTB for C and py.

yaqwsx, 2020-05-14:
You are more experienced in this area and by briefly looking, it looks nice. So, go for it and let's use it.

Closed 2020-05-18.

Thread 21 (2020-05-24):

Periferie na tábor

Tasssadar, 2020-05-24:
Seznam toho, co musí fungovat na Robotku na tábor (i.e. co je potřeba prioritizovat):

**STM:**
- [x] Vypínání, zapínání tlačítka
- [x] Tunel USB na desce -> programování ESP
- [x] Vypínání ze SW
- [x] Napětí na baterii, samovypínání
- [x] Watchdog ESP32 (jestli nespadlo, nezaseklo se)
- [x] Ledky
- [x] Tlačítka
- [x] Motory
- [x] Enkodéry
- [x] Ultrazvuk
- [x] Serva
- [x] Piezo

**ESP32**
- [x] Inteligentní ledky
- [x] ČínaČára senzory

dzarda, 2020-05-24:
Aha pardon, tohle už je výběr a checkboxy mají signalizovat dokončenost...

Closed 2020-07-16.

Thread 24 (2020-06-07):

Zprovoznit programování přes tunel

dzarda, 2020-06-07:
USB tunel už je v STM implementován pomocí dmitrystu/libusb_stm32. Má to ale lehké mouchy:
- V downstream kanálu dochází ke ztrátě dat, když se naráz pošle víc jak 64b (velikost EP). Řešeno v https://github.com/dmitrystu/libusb_stm32/issues/51
- Je nastaveno fixně 115200, lze řešit v `cdc_control ... case USB_CDC_SET_LINE_CODING:`
- UART je stále aktivní nezávisle na připojení CDC

Asi nejdřív třeba vyzkoušet, jestli to v aktuálním stavu už náhodou nejde naprogramovat.

Tasssadar, 2020-06-08:
Ano, a chtěl bych tam přidat i to nastavování rychlosti UARTu, jinak to bude těch 115200 při programování brzdit.

cednik, 2020-06-08:
To by bylo super 👍
Jinak při ovládání těch pinů je potřeba implementovat následující tabulku [[1](https://dl.espressif.com/dl/schematics/esp32_devkitc_v4-sch.pdf)]:
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

Pak je potřeba si pohlídat úroveň na pinech [[2](https://www.espressif.com/sites/default/files/documentation/esp32-wroom-32_datasheet_en.pdf#4)]
- STM PB15(SPI_MOSI/iLed) - ESP IO12 (MTDI/iLed): LOW
- STM v1.0 PC11(UART4_RX/control) v1.1 PD9(UART4_RX/control) - ESP IO2: LOW

Closed 2020-06-15.

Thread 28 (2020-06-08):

hw_v1.1 changes

cednik, 2020-06-08:
- [x] Posunout dráhy měření proudu u serv dál od elektrolytů
- [x] Upravit pinout
- [x] Opravit popisky po změně pinoutu
- [x] Zmenšit zapínací kondenzátory (C5 100 nF, C6 2.2 uF)
- [x] Opravit fungování zapínacího tlačítka bez připojené baterky (napájení z USB)
- [x] Přidat Bmid na svorkovnici
- [ ] ~~Přidat rezistor mezi STM a power~~
- [x] Posunout součástky dál od pinheadů, kvůli pájení
- [x] Opravit masku u DRV8833 center padu
- [x] Zvětšit testpoit GND tak, aby do něj šel zapájet pinhead
- [x] Přesunout popisky pod piezzem
- [x] Nahradit GND_SEPARATOR cutout polygonem
- [x] Zmenšit velikost nastavovacích propojek
- [x] Upravit polygony napájení serv
- [ ] ~~Posunout testpointy dál od kondenzátorů~~ Není na to místo a stejně se k nim poleze zhora
- [x] Zkontrolovat thermaly
- [x] Upravit rozlití mědi kolem upevňovacích otvorů
- [x] Lehce roztáhnout piny USB-C
- [x] (Prohodit micro USB pinheadem, aby bylo místo na kabel vedle USB-C)
- [x] (Vytáhnout buzzer na pinhead)
- [x] (Vytágnout TP62 zpod ESP)
- [x] (Přidat tranzistor na zapínání iLed step-downu)
- [x] (Přehodit I2C na konektoru pro expandér)

yaqwsx, 2020-06-09:
[ ] Zvážit odebrání grafiky na vstvách tPlace a bPlace ve footprintech. Podle [tohoto odkazu](https://electronics.stackexchange.com/questions/186324/what-is-the-difference-between-tplace-and-tdocu-layers-in-eagle-pcb) jsou tPlace a bPlace míněny jako vrstvy silkscreenu a KiCAD import je tak uvažuje. Jedná se o obdélníky okolo koprocesoru:

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

yaqwsx, 2020-06-09:
- [ ] Zvážit nepoužít mezery pro zarovnání textu, ale mít každý sloupeček jako samostatý text; rozbíjí KICAD import kvůli lehce jinému fontu:

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

cednik, 2020-06-09:
- [ ] Popisky svorkovnice zezadu (zepředu pod ní nejsou vidět)
- [ ] Přidat přepěťovou ochranu na měření prostředního článku

cednik, 2020-06-15:
- [ ] Připojit gate Q8 na ESP_EN - fix pull-upu na IO12.

dzarda, 2020-06-17:
[ ] Zvážit přidání pájecích ploch zboku USB konektorů pro lepší odolnost

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

cednik, 2020-07-08:
Verze v1.1 vyrobena, zavírám.

Closed 2020-07-08.

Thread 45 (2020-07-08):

HW v1.1 issues

cednik, 2020-07-08:
- [x] rezistory R20-R23 od VUSB a ESP_+5V power LEDek mají být 2k2 (momentálně 1k)
- [x] odpojit 3V3_EN od diody D11 - dokud neběží 3V3, dioda drží EN k zemi, tudíž stabilizátor nenastartuje a deska nejde zapnout
- [ ] ~~nepoužívat jednopinové pinheady - blbě se pájí~~ moc peněz za málo muziky - stejně je nikdo nepoužívá (tudíž neosazuje)
- [x] zmenšit vrtání konektorů pro motory (a asi i inteligentní serva) - zbytečně to kloktá
- [x] konektory pro inteligentní serva jsou o milimetr tlustší, než jejich footprint v eaglu, a nevlezou se kvůli konektorům pro ultrazvuky
- [x] zvětšit pájecí plošku (mezikruží) konektorů pro inteligentní serva - strašně blbě se chytá cín k desce
- [x] ~~zvážit změnu CR2032 za menší baterku - je drahá (ale pozor, aby bylo dostupné pouzdro)~~ IKEA
- [ ] ~~přesunout TP1 a TP18 zpod step-downu~~ moc peněz za málo muziky
- [x] nachystat prostor pro gravírování jména vlastníka přímo na místě
- [x] dostat součástky ještě dál od pájecích plošek (a třeba u ESP nechat všechny jen z jedné strany dutinek, ať se po druhé straně dá jet pájkou bezpečně)
- [x] odmaskovat někde na kraji kus země na chycení země od osciloskopu

cednik, 2020-10-11:
Opraveny odpory, dioda a konektory.
Přidán prostor pro jméno vlastníka (i když s gravírováním se bude muset opartně, protože by to bylo do +5V mědi).
Přidán kus odmaskované země pro chycení sondy osciloskopu.
Nejmenší SMD součástky posunuty dál od pinheadů (aby je děti omylem neodpájely) - rezistory kolem dutinek ESP32, u SPI a dělič měření baterky.

Jednopinové pinheady stejně téměř nikdo neosazuje, tudíž jejich překreslení je spousta téměř zbytečné práce.
Stejně tak přesun testpointů by byl značně netriviální a z druhé strany desky se k nim dá stále dostat.
Baterky se dají koupit dostatečně levně.

Closed 2020-10-11.

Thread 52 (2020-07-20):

Defaultní 5V zdroj

dzarda, 2020-07-20:
Deska by imho měla mít výchozí zdroj pěti voltů. Práce s levnými stepdowny zdá se mi nešťastná pro většinu případů.

yaqwsx, 2020-07-21:
V rámci https://github.com/RoboticsBrno/RB0004-NeopixelBooster jsme s Martinem Kousalem navrhli 3A step-down čistě z součástek z JLCPCB, který se cenově vleze do 1 USD a plochou taktéž není náročný.

cednik, 2020-07-21:
Bylo by to krásné, ale i když malý, jsou to 2 cm², které tam teď nejsou.
Znamená to desku celou překopat.
Jsem pro to udělat a zároveň implementovat #51.
Jen se musíme rozhodnout, jestli vznikne RBCX 2.0, nebo RBCX+ :-D

dzarda, 2020-07-21:
Za mě stačí bump na verzi 1.2 :P

A nestačilo by čistě náhodou prostě LDO?

cednik, 2020-07-21:
Přesně tak. LDO by nejspíš stačilo na napájení STM, ale na ostatní periférie (včetně ESP) už chceš spínaný zdroj.
Pouhá výměna stabilizátoru a ostatní moje issue k verzi 1.1 ( #45 )  stačí na v1.2. Přidání nabíjení už je podle mě moc velký zásah.

dzarda, 2021-05-19:
Skvělý by byl i OC výstup, kterým by šlo uživatele informovat o možnosti osadit další stepdown modul :P

cednik, 2021-05-19:
Co myslíš OC výstupem a při jaké příležitosti bys chtěl takovou informaci podávat?

dzarda, 2021-05-19:
Myslím nadproud na stepdownu. Podávat by bylo vhodné až uživatelovi "operátorovi", společně s např. napětím baterky

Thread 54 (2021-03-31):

Real time clock

dzarda, 2021-03-31:
Jirka potřebuje rozchodit RTC na naší úžasné desce.

- Přidat PB zprávy
- Přidat RTC driver
- Otestovat RTC, změřit odběr...

dzarda, 2021-04-05:
RTC nemá kalendářovou logiku, ale umí pouze monotonicky čítat. @Tasssadar Stačí umět čítat sekundy?

- Set zpráva nastaví sekundy (implikuje inicializaci)
- Get zpráva přečte sekundy (nebo 0, když nemáme baterku/není inicializování.

yaqwsx, 2021-04-05:
Nestačilo by nám mít unix epochu?

dzarda, 2021-04-05:
Jo, však to je ono. Klient určí hodnotu v Set funkci, od toho to pak počítá sekundy. Naskýtá se mít to jako unix timestamp

Tasssadar, 2021-04-05:
To zní jakože by mělo stačit, "set" může nastavit buďto epoch, nebo prostě cokoliv. Vyšší přesnost než vteřiny neumí?

dzarda, 2021-04-05:
Umí to přesnost jakou chceš, ale má to jen 32 bitů

dzarda, 2021-04-06:
Změřeno 1,26uA

cednik, 2021-04-06:
>
>
> Umí to přesnost jakou chceš, ale má to jen 32 bitů

Běží to z krystalového oscilátoru 32.768 kHz, tudíž 1 sekunda je myslím nejvíc smysluplný časový úsek, který má smysl z toho dolovat. Ale předděličku si můžu nastavit od 1 do 1 048 576 (2^20), takže kdyby někdo moc chtěl, může to být přesnější.
Ovšem pak se špatně počítá ta epocha, když to může přetéct, zatím co procesor nemá šťávu :-)

cednik, 2021-04-06:
Kromě get a set bych ještě poprosil o alarm.get/set/enable/disable.
Ono to totiž pak umí přes POWER pin (PC13) celé RBCX v nastavený čas zapnout :-)

dzarda, 2021-04-06:
Najs, alarm udělám

dzarda, 2021-04-13:
Alarm bude vhodné nastavovat asi jako parametr `powerOff` příkazu, protože nastavení `ASOE` tu nohu okamžitě stahuje, čímž vypíná desku.

Protože to stahuje dolů furt i po vypnutí, zapnutí tlačítkem nefunguje - jen problikne a zase se vypne. Musím zkusit, jestli během probliknutí nastartuje proc a jestli je čas tu nohu odpoutat.

cednik, 2021-04-14:
Mám za to, že jsem to zkoušel a že to fungovalo. Bohužel, v testovací větvy v commitech jsem to nenašel :-(

Nastavovat alarm jako parametr powerOff klidně, ale asi se mi to moc nelíbí jako jediná možnost - asi si chci umět nastavit alarm dopředu, dřív, než budu zařízení vypínat. Nehledě na možnosti že se to vypne samo kvůli vybité baterce, nebo jejímu odpojení.
Nemůže si STM nastavený alarm pamatovat a až při vypínání nastavit správně power pin? (Ať už se vypne příkazem, nebo poklesem napětí na baterce, ke kterému dojde i při jejím odpojení.)

dzarda, 2021-04-14:
Jasně, musí si to vlastně pamatovat stejně kvůli těm průběžným vypnutím/zapnutím...

> zkoušel a že to fungovalo

Myslíš tu insta alarm deaktivaci při startu?

cednik, 2021-04-14:
Zkoušel jsem, jestli to tím jde zapnout a šlo to. Jestli jsem dělal deaktivaci si bohužel nepamatuji. Nicméně si pamatuji, že to umělo dělat jen pulz, nikoli držet úroveň, tak jsem ji asi dělat musel.

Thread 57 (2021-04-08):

Enkodérové vstupy jako koncáky

dzarda, 2021-04-08:
Jirka měl nápad použít motorové vstupy enkodéru jako koncáky. Mohlo by to být hardwarově jednoduché řešení, jak řešit pohyb osy bez enkodéru. (Kromě vazby proudem)

IMHO by to elektricky neměl být problém. Máme na ENC vstupech super pullupy a ochrany, takže koncák jen stáhne k zemi.

dzarda, 2021-04-22:
Tak Jirka by si přál umět vyčítat stav těchto pinů i "obecněji".

Use case je umět rotační osu homovat na konkrétní stav ENC pinů...

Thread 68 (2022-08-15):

Lepší motor driver

dzarda, 2022-08-15:
Stálo by za zvážení, zda do další revize nedát proudově lepší drivery motorů

yaqwsx, 2022-08-15:
Na Serviu používáme **DRV8870**
 - jednokanálový
 - 3.6A špičkově
 - 6.5-45V, má to interní omezení proudu.

 Já sním o **DRV8874**:
- které je jednokanálové,
- 6A špičkově,
- 4.5-37V
- umí měřit proud na úbytku na interním MOSFETU a zdrcadlit ho (tj. nepotřebuje current shunt, který topí)
- bohužel, dlouhodobě nedostupné. Mouser naskladní až 8/3/2023
- zatím se dá koupit za 2k devkit: https://cz.mouser.com/ProductDetail/Texas-Instruments/DRV8874EVM?qs=mAH9sUMRCtsW213NeE2uzA%3D%3D

dzarda, 2022-08-23:
U DRV8833 (co tam teď je) se mluví o paralelním zapojení výstupů. Pokud by se nám povedlo elegantně umožnit spojení výstupů na desce (nebo kabelem), mohla by to být cesta k řízení dvou lepších motorů.

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

JarekParal, 2022-08-23:
Mám za to, že jsme s tím při návrhu RBCX (možná už při RBC) počítali jako s možností jak uřídit silnější motory. Ale myslím, že žádná speciální příprava na DPS udělaná není.

cednik, 2022-08-23:
Taky si myslím, že se s tím jako s možností počítalo.
Na desce opravdu žádná příprava není a ani nevím, kam by se případně vlezla.
Softwarově je potřeba zaručit, že budou opravdu generována stejná PWM pro obě půlky (nevím, jestli teď FW v STM používá u časovaču dvojité bufferování?). Hardwarově doporučuji dva samostatné kabely, spojené až u motoru - v případě omylem nastavených různých PWM budou sloužit jako odpor a indukčnost a aspoň lehce omezí zkratový proud.

dzarda, 2022-08-23:
Double buf nevím, ale zřejmě je řešitelné. Double kabely zní asi dobře.

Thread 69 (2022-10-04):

Režim motor-otrok

dzarda, 2022-10-04:
V případě zapojení dvou motorů na stejnou fyzickou osu (strana robota) může být výhodné použít jen jeden enkodér. Tehdy je třeba do obou motorů krmit stejné PWM s použitím jen jednoho enkodéru.

dzarda, 2022-10-04:
Důležité zajistit identický výstup PWM pro případ paralelizace výstupů do 1 motoru (Timer double-buf)

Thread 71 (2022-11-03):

Napájecí/stepdown modul

vachajirka, 2022-11-03:
Vznikna nabíjecí/stepdown modul, který bude zapojen do napájecího systému desky. Budeme chtít nabíjet baterku z USB. Modul bude
- USB budeme chtít přes QC na vyšší napětí
- VBUS_DET zaclampovat
- Střed baterky přidat na pinhead
- Vytěžit signál pro charge-enable
- Je třeba prozkoumat možnost implementace QC na hlavním koprocesoru (potřeba signál/y pro QC)

Když je ESP vypnuté, tak chceme být schopní nabíjet.

yaqwsx, 2022-11-03:
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

@dzarda: Tady jsou dvě mé implementace QC. Ta první funguje 100% (je vlastně i na původní nabíječce k RBCX), ta druhá by měla také (je to nápad od @cednik) ale netestováno (ale mám k dipozici desku, do které stačí jen QC logiky naprogramovat).

Zajímavé odkazy:
- https://github.com/Crypter/QC3Client/
- http://blog.deconinck.info/post/2017/08/09/Turning-a-Quick-Charge-3.0-charger-into-a-variable-voltage-power-supply

dzarda, 2022-11-06:
@cednik bude snad přímočařejší najít 3 signály (snad 2 QC + 1 charge-enable), než dávat nabíjecí procesor.

yaqwsx, 2022-11-06:
A což takhle přecijen přidat nějaký mini procesor, který by poslouchal na 1-wire? Nebo si prachsprostě na QC použít posuvný registr.

PS: To, co jsem nezmínil - určitě je třeba pro implementaci QC ještě měřit napětí na VBUS. Protože QC3 funguje po inkrementech.

dzarda, 2022-11-06:
Pokud nenajdem piny, tak expander/pos. registr zní dobře. Mohlo by být na I2C.

Měření vbus je pravda, asi logicky může nahradit VBUS_DET

dzarda, 2022-11-08:
Když je vypnuto a zapojím nabíječku, mělo by začít nabíjet.

yaqwsx, 2022-11-08:
Zajímavé téma ohledně čínských USB-PD/QC triggerů: https://www.eevblog.com/forum/projects/usb-pdqc-trigger-ic-anybody-know-what-these-aexp-modules-use/

yaqwsx, 2022-11-08:
...a možná by se dal udělat reverse engineering tohoto: https://www.aliexpress.com/item/1005004004234197.html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

yaqwsx, 2022-11-08:
A další várka IC (dostupné z LCSC a tedy i JLC PCB):
- 50 centů v kusovce: https://datasheet.lcsc.com/lcsc/2111121930_Legendary-LDR6328_C2919630.pdf
- pouze PD: https://datasheet.lcsc.com/lcsc/2006111335_INJOINIC-IP2721_C603176.pdf

dzarda, 2022-11-22:
Kandidát na 5V stepdown https://www.lcsc.com/product-detail/DC-DC-Converters_Texas-Instruments-TPS54623RHLR_C560970.html

dzarda, 2022-12-11:
Kandidát na nabíječku https://www.digikey.com/en/products/detail/monolithic-power-systems-inc/MP2651GVT-0000-Z/16688711

dzarda, 2022-12-13:
@yaqwsx Mohl bys mi prosím pomoct ještě s výběrem konkrétního QC/PD řešení?

Myslím, že USB BC rozpoznání nepotřebujeme. Asi stačí mít na začátku pokus o komunikaci...

```
pokusit se dělat PD/C current
pokusit se enumerovat USB
když USB enumerace vyšla:
   sosat 500mA (nebo víc pokud PD/C current vyšlo)
jinak když nevyšlo PD:
   pokusit se dělat QC
   když nevyšlo QC:
      sosat 500mA
```

Zajímavě vypadá CH224. Musel by se asi  od USB odstřihnout/začít napájet až po neúspěšné enumeraci,

LDR6321 taky umí asi velký věci. Dokonce tam vidím nějaký "EN" piny, ale nenašel jsem ani zmínku, jestli to má skutečně nějakou enable logiku.

yaqwsx, 2022-12-13:
Navrhuji:
- sehnat vzorky od obojího
- postavit s nějakým discovery kitem prototyp.
Datasheety totiž vypadají docela mlhavě a nechce se mi riskovat, že nakreslíme desku, která nebude fungovat. Přemýšlím, jestli by náš problém ještě neřešil nějaký IC pro USB mux, který by nám DP/DM přepínal mezi procesorem a IC (anebo prostě QC handlovat v našem procesoru).

S procesem, který jsi napsal výše souhlasím a dělal bych to stejně.

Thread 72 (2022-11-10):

RBCX 1.3 featury

vachajirka, 2022-11-10:
- Využili bychom 6-ti vrstvou desku, abychom minimalizovali zásah do návrhu
- QC a možná i PD (ideálně integrovaný PD Sink IC typu STUSB4500 nebo PD PHY typu FUSB302)
- Nabíjecí/stepdown řešení viz. #71 , všechny stepdowny nahradit
- USB-C s lepším mechanickým jištěním
- Micro asi pryč

dzarda, 2022-11-19:
Import do Kicadu 6.0.9 funguje na první pohled překvapivě dobře. Zde regiony, které asi zasaženy.
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

yaqwsx, 2022-11-20:
Když napíšeš přesně co nefunguje, tak bychom to mohli doprogramovat.

dzarda, 2022-11-20:
Špatně jsem se vyjádřil, zatím jsem na žádné problémy nenarazil. Ten region je prostě to, kde očekávám změny.

dzarda, 2022-11-21:
Tohle vypadá hodně dobře pro PD+QC https://www.electronicsweekly.com/news/products/power-supplies/usb-type-c-sink-controllers-for-pd3-0-pps-2022-10/

yaqwsx, 2022-11-21:
Dívám se do datasheetu a nevidím tam zmínku o QC.

dzarda, 2022-11-21:
Doufal jsem, že půjde využít GPIO piny jako expandér :')

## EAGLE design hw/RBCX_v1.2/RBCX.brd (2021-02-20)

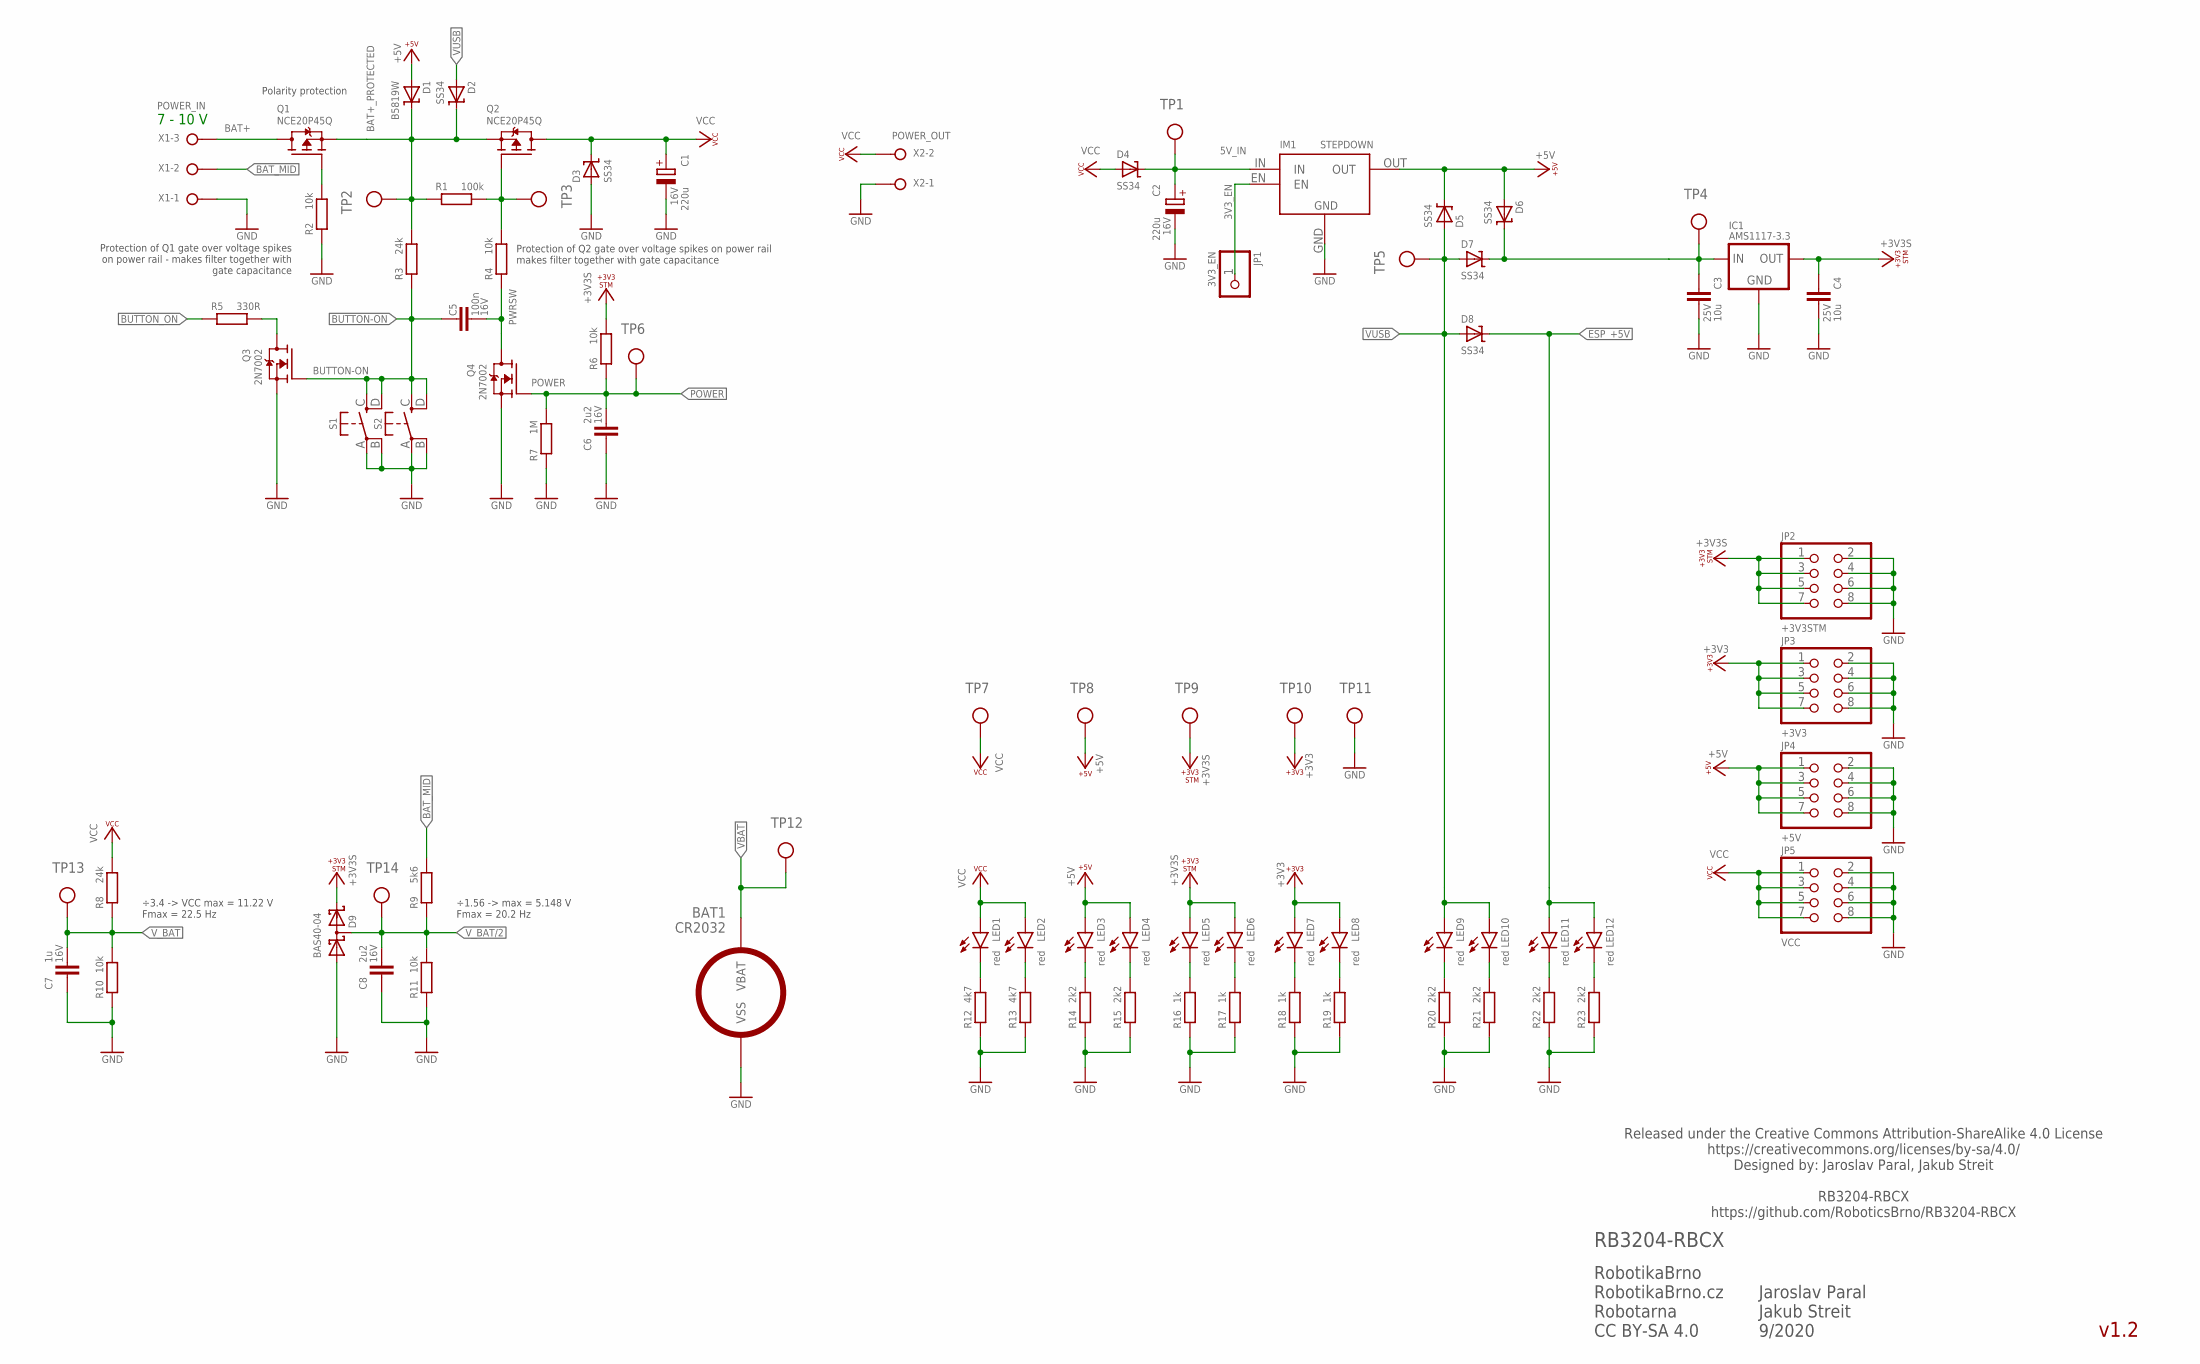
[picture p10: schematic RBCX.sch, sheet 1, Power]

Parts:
BAT1: CR2032; SMD-BAT-CR2032-BS-6-1
C1, C2: 220u; E5-10,5; VOLTAGE 16V
C3, C4: 10u; C0805; VOLTAGE 25V
C5: 100n; C0402; VOLTAGE 16V
C6, C8: 2u2; C0603; VOLTAGE 16V
C7: 1u; C0402; VOLTAGE 16V
D1: B5819W; SOD123; LCSC_ID C305445
D2, D3, D4, D5, D6, D7, D8: SS34; SMA
D9: BAS40-04; SOT23
IC1: AMS1117-3.3; SOT223
IM1: STEPDOWN
JP1: 3V3_EN; 1X01
JP2: +3V3STM; 2X04
JP3: +3V3; 2X04
JP4: +5V; 2X04
JP5: VCC; 2X04
LED1, LED2, LED3, LED4, LED5, LED6, LED7, LED8, LED9, LED10, LED11, LED12: red; CHIPLED_0603
Q1, Q2: NCE20P45Q; MLP3.3X3.3_HS; LCSC_ID C193354
Q3, Q4: 2N7002; SOT23; LCSC_ID C8545
R1: 100k; R0402
R2, R4, R6, R10, R11: 10k; R0402
R3, R8: 24k; R0402
R5: 330R; R0402
R7: 1M; R0402
R9: 5k6; R0402
R12, R13: 4k7; R0402
R14, R15, R20, R21, R22, R23: 2k2; R0402
R16, R17, R18, R19: 1k; R0402
S1, S2: TS-1187A-C-C-B; TS-1187A
TP1, TP2, TP3, TP4, TP5, TP6, TP7, TP8, TP9, TP10, TP12, TP13, TP14: TP_06MM; TP_06
TP11: TP_08MM; TP_08
X1: POWER_IN; W237-133
X2: POWER_OUT; W237-132

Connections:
3V3_EN: IM1.EN, JP1.1
3V3_IN: C3.2, D6.C, D7.C, IC1.3 (IN), TP4.P$1
5V_IN: C2.+, D4.C, IM1.IN, TP1.P$1
+3V3: JP3.1, JP3.3, JP3.5, JP3.7, LED7.A, LED8.A, TP10.P$1; also elsewhere on the board
+3V3S: C4.2, D9.2 (C2), IC1.2 (OUT), IC1.4 (OUT), JP2.1, JP2.3, JP2.5, JP2.7, LED5.A, LED6.A, R6.2, TP9.P$1; also elsewhere on the board
+5V: D1.A, D5.C, D6.A, IM1.OUT, JP4.1, JP4.3, JP4.5, JP4.7, LED3.A, LED4.A, TP8.P$1; also elsewhere on the board
BAT+: Q1.5 (D), Q1.6 (D), Q1.7 (D), Q1.8 (D), Q1.9 (D), X1.3
BAT+_PROTECTED: D1.C, D2.C, Q1.1 (S), Q1.2 (S), Q1.3 (S), Q2.1 (S), Q2.2 (S), Q2.3 (S), R1.1, R3.2, TP2.P$1
BAT_MID: R9.2, X1.2
BUTTON-ON: C5.2, Q3.1 (G), R3.1, S1.C (S), S1.D (S1), S2.C (S), S2.D (S1); also elsewhere on the board
BUTTON-ON-LV: Q3.3 (D), R5.2
BUTTON_ON: R5.1; also elsewhere on the board
ESP_+5V: D8.C, LED11.A, LED12.A; also elsewhere on the board
GND: BAT1.VSS, C1.-, C2.-, C3.1, C4.1, C6.2, C7.2, C8.2, D3.A, D9.1 (A1), IC1.1 (GND), IM1.GND, JP2.2, JP2.4, JP2.6, JP2.8, JP3.2, JP3.4, JP3.6, JP3.8, JP4.2, JP4.4, JP4.6, JP4.8, JP5.2, JP5.4, JP5.6, JP5.8, Q3.2 (S), Q4.2 (S), R2.1, R7.1, R10.1, R11.1, R12.1, R13.1, R14.1, R15.1, R16.1, R17.1, R18.1, R19.1, R20.1, R21.1, R22.1, R23.1, S1.A, S1.B (P1), S2.A, S2.B (P1), TP11.P$1, X1.1, X2.1; also elsewhere on the board
POWER: C6.1, Q4.1 (G), R6.1, R7.2, TP6.P$1; also elsewhere on the board
PROT_GATE: Q1.4 (G), R2.2
PWRLED_+3V3: LED7.C, R18.2
PWRLED_+3V3B: LED8.C, R19.2
PWRLED_+3V3S: LED5.C, R16.2
PWRLED_+3V3S_B: LED6.C, R17.2
PWRLED_+5V: LED3.C, R14.2
PWRLED_+5VESP: LED11.C, R22.2
PWRLED_+5VESP_B: LED12.C, R23.2
PWRLED_+5V_B: LED4.C, R15.2
PWRLED_VCC: LED1.C, R12.2
PWRLED_VCC_B: LED2.C, R13.2
PWRLED_VUSB: LED9.C, R20.2
PWRLED_VUSB_B: LED10.C, R21.2
PWRSW: C5.1, Q4.3 (D), R4.1
PWRSW_GATE: Q2.4 (G), R1.2, R4.2, TP3.P$1
VBAT: BAT1.VBAT, TP12.P$1; also elsewhere on the board
VCC: C1.+, D3.C, D4.A, JP5.1, JP5.3, JP5.5, JP5.7, LED1.A, LED2.A, Q2.5 (D), Q2.6 (D), Q2.7 (D), Q2.8 (D), Q2.9 (D), R8.2, TP7.P$1, X2.2; also elsewhere on the board
VUSB: D2.A, D5.A, D7.A, D8.A, LED9.A, LED10.A, TP5.P$1; also elsewhere on the board
V_BAT: C7.1, R8.1, R10.2, TP13.P$1; also elsewhere on the board
V_BAT/2: C8.1, D9.3 (C1A2), R9.1, R11.2, TP14.P$1; also elsewhere on the board

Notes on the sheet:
Polarity protection
÷3.4 -> VCC max = 11.22 V Fmax = 22.5 Hz
v1.2
RobotikaBrno RobotikaBrno.cz Robotarna CC BY-SA 4.0
RB3204-RBCX
Released under the Creative Commons Attribution-ShareAlike 4.0 License https://creativecommons.org/licenses/by-sa/4.0/ Designed by: Jaroslav Paral, Jakub Streit RB3204-RBCX https://github.com/RoboticsBrno/RB3204-RBCX
Jaroslav Paral Jakub Streit 9/2020
÷1.56 -> max = 5.148 V Fmax = 20.2 Hz
Protection of Q1 gate over voltage spikes on power rail - makes filter together with gate capacitance
Protection of Q2 gate over voltage spikes on power rail makes filter together with gate capacitance
7 - 10 V

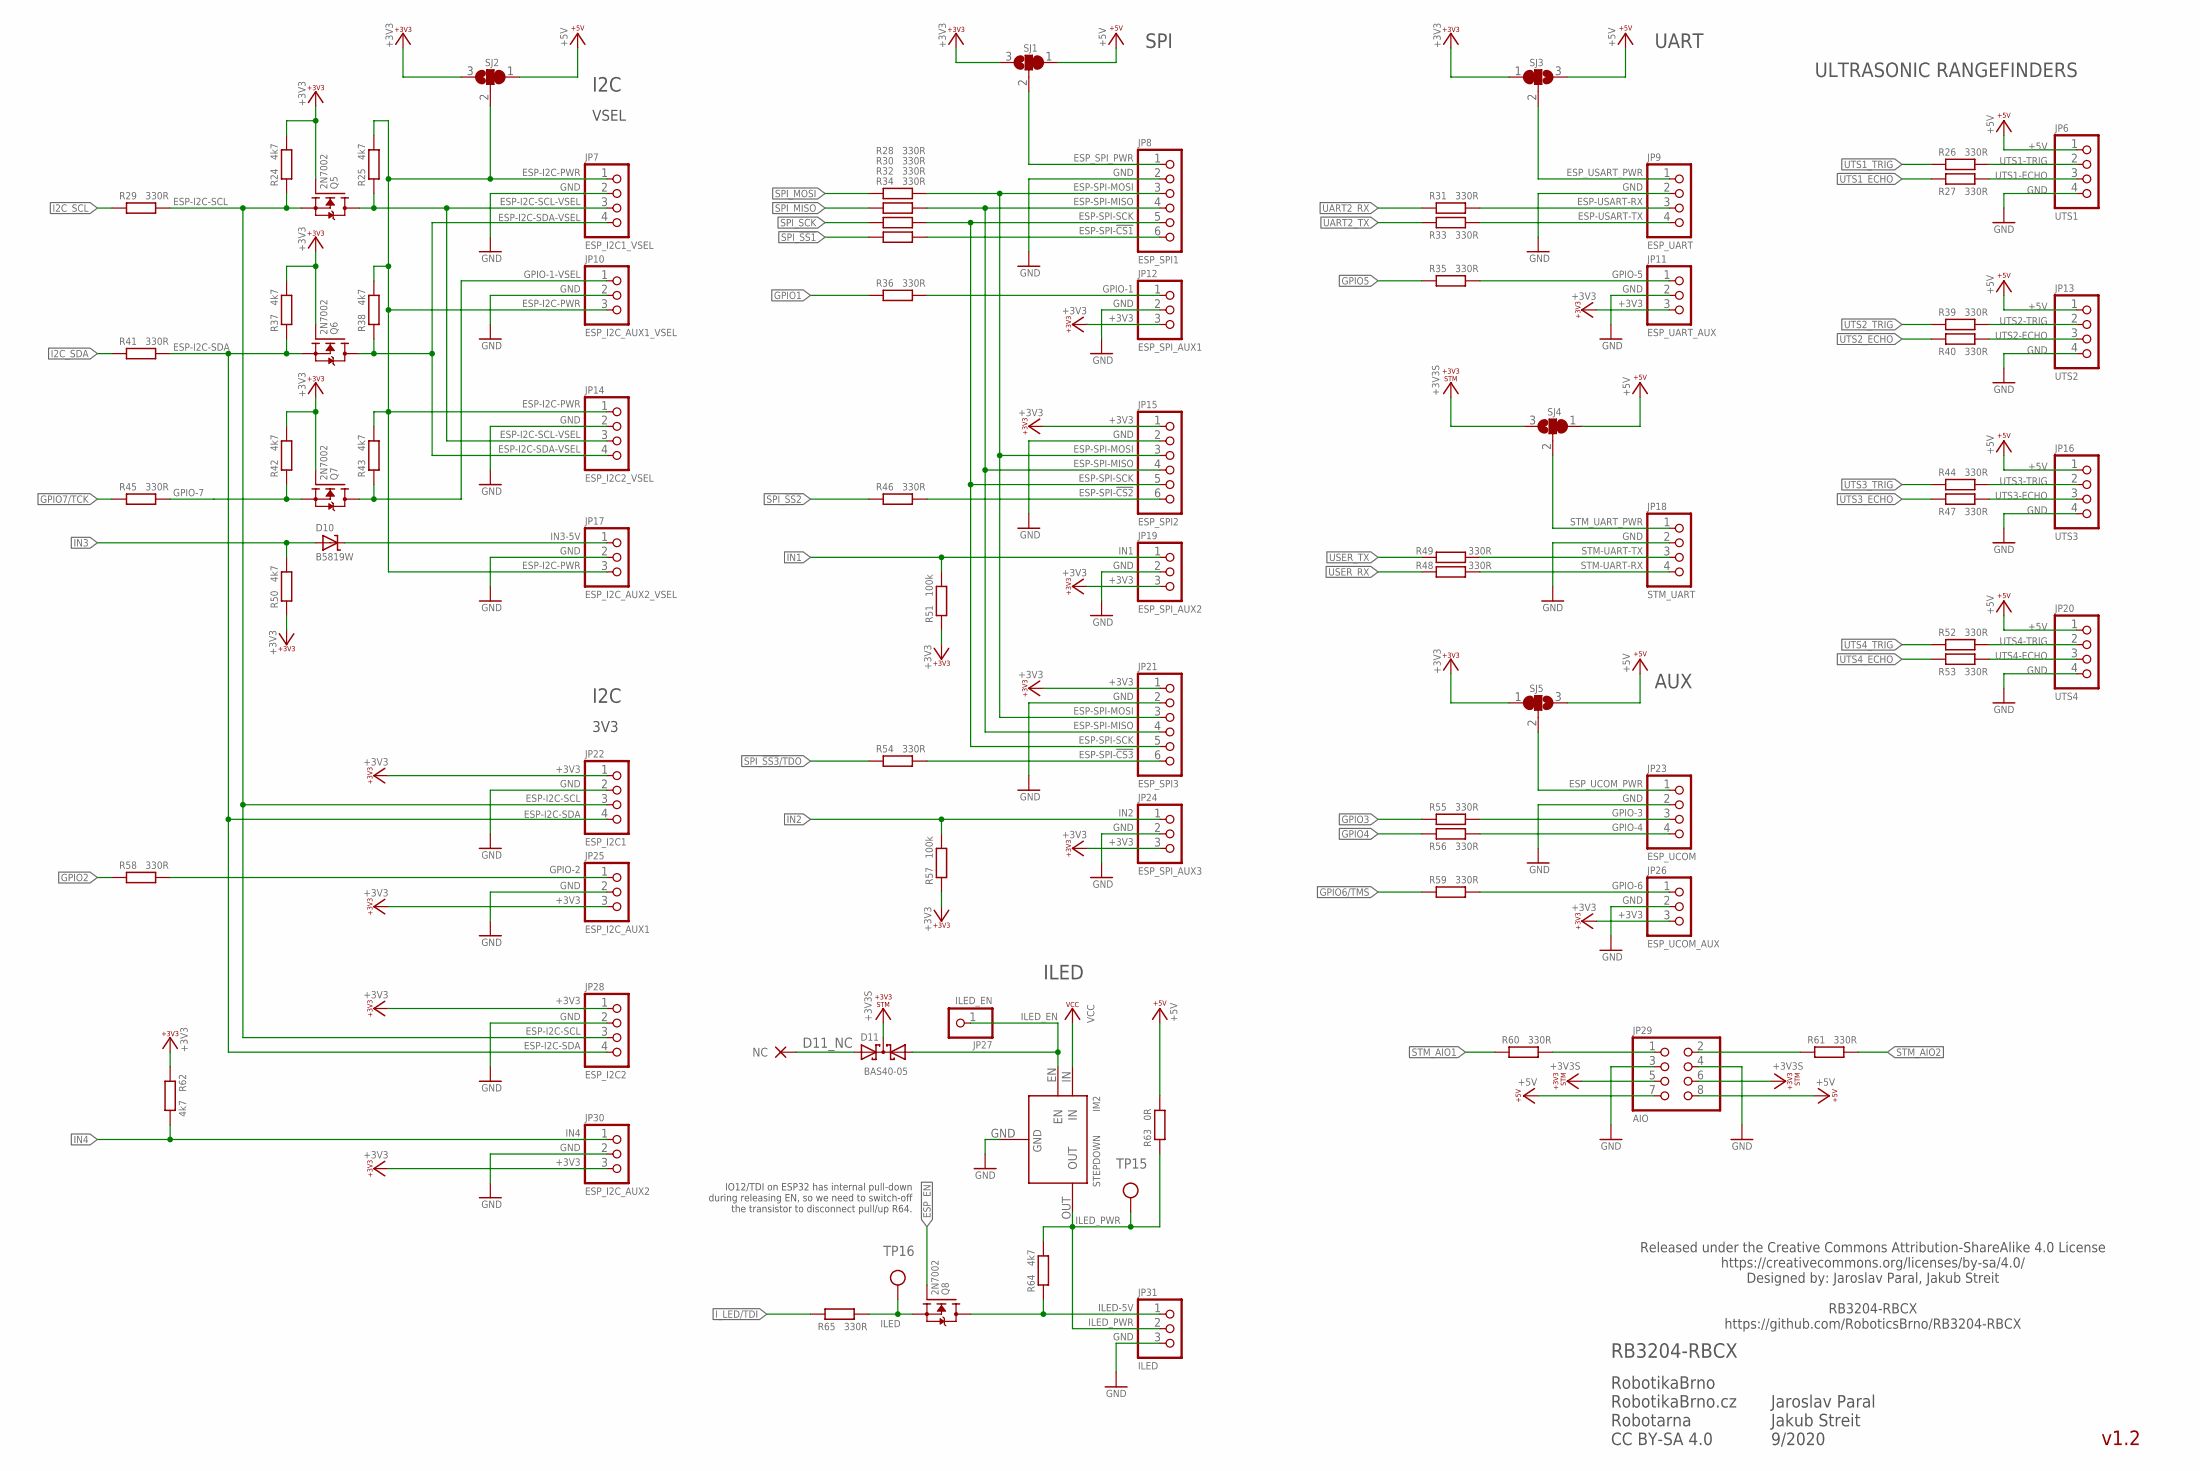
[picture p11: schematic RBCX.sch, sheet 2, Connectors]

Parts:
D10: B5819W; SOD123; LCSC_ID C305445
D11: BAS40-05; SOT23
IM2: STEPDOWN
JP6: UTS1; 1X04
JP7: ESP_I2C1_VSEL; 1X04
JP8: ESP_SPI1; 1X06
JP9: ESP_UART; 1X04
JP10: ESP_I2C_AUX1_VSEL; 1X03
JP11: ESP_UART_AUX; 1X03
JP12: ESP_SPI_AUX1; 1X03
JP13: UTS2; 1X04
JP14: ESP_I2C2_VSEL; 1X04
JP15: ESP_SPI2; 1X06
JP16: UTS3; 1X04
JP17: ESP_I2C_AUX2_VSEL; 1X03
JP18: STM_UART; 1X04
JP19: ESP_SPI_AUX2; 1X03
JP20: UTS4; 1X04
JP21: ESP_SPI3; 1X06
JP22: ESP_I2C1; 1X04
JP23: ESP_UCOM; 1X04
JP24: ESP_SPI_AUX3; 1X03
JP25: ESP_I2C_AUX1; 1X03
JP26: ESP_UCOM_AUX; 1X03
JP27: ILED_EN; 1X01
JP28: ESP_I2C2; 1X04
JP29: AIO; 2X04
JP30: ESP_I2C_AUX2; 1X03
JP31: ILED; 1X03
Q5, Q6, Q7, Q8: 2N7002; SOT23; LCSC_ID C8545
R24, R25, R37, R38, R42, R43, R50, R62, R64: 4k7; R0402
R26, R27, R28, R29, R30, R31, R32, R33, R34, R35, R36, R39, R40, R41, R44, R45, R46, R47, R48, R49, R52, R53, R54, R55, R56, R58, R59, R60, R61, R65: 330R; R0402
R51, R57: 100k; R0402
R63: 0R; R1206
SJ1, SJ2, SJ3, SJ4, SJ5: SJ2W_DEFAULT; SJ_2_DEFAULT
TP15, TP16: TP_06MM; TP_06

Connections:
+3V3: JP11.3, JP12.3, JP15.1, JP19.3, JP21.1, JP22.1, JP24.3, JP25.3, JP26.3, JP28.1, JP30.3, Q5.1 (G), Q6.1 (G), Q7.1 (G), R24.2, R37.2, R42.2, R50.1, R51.1, R57.1, R62.1, SJ1.3, SJ2.3, SJ3.1, SJ5.1; also elsewhere on the board
+3V3S: D11.3 (C), JP29.5, JP29.6, SJ4.3; also elsewhere on the board
+5V: JP6.1, JP13.1, JP16.1, JP20.1, JP29.7, JP29.8, R63.2, SJ1.1, SJ2.1, SJ3.3, SJ4.1, SJ5.3; also elsewhere on the board
D11_NC: D11.2 (A2)
ESP-I2C-PWR: JP7.1, JP10.3, JP14.1, JP17.3, R25.2, R38.2, R43.2, SJ2.2
ESP-I2C-SCL: JP22.3, JP28.3, Q5.2 (S), R24.1, R29.2; also elsewhere on the board
ESP-I2C-SCL-VSEL: JP7.3, JP14.3, Q5.3 (D), R25.1
ESP-I2C-SDA: JP22.4, JP28.4, Q6.2 (S), R37.1, R41.2; also elsewhere on the board
ESP-I2C-SDA-VSEL: JP7.4, JP14.4, Q6.3 (D), R38.1
ESP-SPI-!CS1: JP8.6, R34.2
ESP-SPI-!CS2: JP15.6, R46.2
ESP-SPI-!CS3: JP21.6, R54.2
ESP-SPI-MISO: JP8.4, JP15.4, JP21.4, R30.2
ESP-SPI-MOSI: JP8.3, JP15.3, JP21.3, R28.2
ESP-SPI-SCK: JP8.5, JP15.5, JP21.5, R32.2
ESP-USART-RX: JP9.3, R31.2
ESP-USART-TX: JP9.4, R33.2
ESP_EN: Q8.1 (G); also elsewhere on the board
ESP_SPI_PWR: JP8.1, SJ1.2
ESP_UCOM_PWR: JP23.1, SJ5.2
ESP_USART_PWR: JP9.1, SJ3.2
GND: IM2.GND, JP6.4, JP7.2, JP8.2, JP9.2, JP10.2, JP11.2, JP12.2, JP13.4, JP14.2, JP15.2, JP16.4, JP17.2, JP18.2, JP19.2, JP20.4, JP21.2, JP22.2, JP23.2, JP24.2, JP25.2, JP26.2, JP28.2, JP29.3, JP29.4, JP30.2, JP31.3; also elsewhere on the board
GPIO1: R36.1; also elsewhere on the board
GPIO2: R58.1; also elsewhere on the board
GPIO3: R55.1; also elsewhere on the board
GPIO4: R56.1; also elsewhere on the board
GPIO5: R35.1; also elsewhere on the board
GPIO6/TMS: R59.1; also elsewhere on the board
GPIO7/TCK: R45.1; also elsewhere on the board
GPIO-1: JP12.1, R36.2
GPIO-1-VSEL: JP10.1, Q7.3 (D), R43.1
GPIO-2: JP25.1, R58.2; also elsewhere on the board
GPIO-3: JP23.3, R55.2
GPIO-4: JP23.4, R56.2
GPIO-5: JP11.1, R35.2
GPIO-6: JP26.1, R59.2
GPIO-7: Q7.2 (S), R42.1, R45.2
I2C_SCL: R29.1; also elsewhere on the board
I2C_SDA: R41.1; also elsewhere on the board
ILED: Q8.2 (S), R65.2, TP16.P$1
ILED-5V: JP31.1, Q8.3 (D), R64.1; also elsewhere on the board
ILED_EN: D11.1 (A1), IM2.EN, JP27.1
ILED_PWR: IM2.OUT, JP31.2, R63.1, R64.2, TP15.P$1
IN1: JP19.1, R51.2; also elsewhere on the board
IN2: JP24.1, R57.2; also elsewhere on the board
IN3: D10.A, R50.2; also elsewhere on the board
IN3-5V: D10.C, JP17.1
IN4: JP30.1, R62.2; also elsewhere on the board
I_LED/TDI: R65.1; also elsewhere on the board
SPI_!SS1: R34.1; also elsewhere on the board
SPI_!SS2: R46.1; also elsewhere on the board
SPI_!SS3!/TDO: R54.1; also elsewhere on the board
SPI_MISO: R30.1; also elsewhere on the board
SPI_MOSI: R28.1; also elsewhere on the board
SPI_SCK: R32.1; also elsewhere on the board
STM-AIO1: JP29.1, R60.2
STM-AIO2: JP29.2, R61.1
STM-UART-RX: JP18.4, R49.2
STM-UART-TX: JP18.3, R48.2
STM_AIO1: R60.1; also elsewhere on the board
STM_AIO2: R61.2; also elsewhere on the board
STM_UART_PWR: JP18.1, SJ4.2
UART2_RX: R31.1; also elsewhere on the board
UART2_TX: R33.1; also elsewhere on the board
USER_RX: R49.1; also elsewhere on the board
USER_TX: R48.1; also elsewhere on the board
UTS1-ECHO: JP6.3, R27.2
UTS1-TRIG: JP6.2, R26.2
UTS1_ECHO: R27.1; also elsewhere on the board
UTS1_TRIG: R26.1; also elsewhere on the board
UTS2-ECHO: JP13.3, R40.2
UTS2-TRIG: JP13.2, R39.2
UTS2_ECHO: R40.1; also elsewhere on the board
UTS2_TRIG: R39.1; also elsewhere on the board
UTS3-ECHO: JP16.3, R47.2
UTS3-TRIG: JP16.2, R44.2
UTS3_ECHO: R47.1; also elsewhere on the board
UTS3_TRIG: R44.1; also elsewhere on the board
UTS4-ECHO: JP20.3, R53.2
UTS4-TRIG: JP20.2, R52.2
UTS4_ECHO: R53.1; also elsewhere on the board
UTS4_TRIG: R52.1; also elsewhere on the board
VCC: IM2.IN; also elsewhere on the board

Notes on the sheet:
v1.2
RobotikaBrno RobotikaBrno.cz Robotarna CC BY-SA 4.0
RB3204-RBCX
Released under the Creative Commons Attribution-ShareAlike 4.0 License https://creativecommons.org/licenses/by-sa/4.0/ Designed by: Jaroslav Paral, Jakub Streit RB3204-RBCX https://github.com/RoboticsBrno/RB3204-RBCX
Jaroslav Paral Jakub Streit 9/2020
I2C
SPI
UART
VSEL
3V3
ILED
ULTRASONIC RANGEFINDERS
AUX
IO12/TDI on ESP32 has internal pull-down during releasing EN, so we need to switch-off the transistor to disconnect pull/up R64.

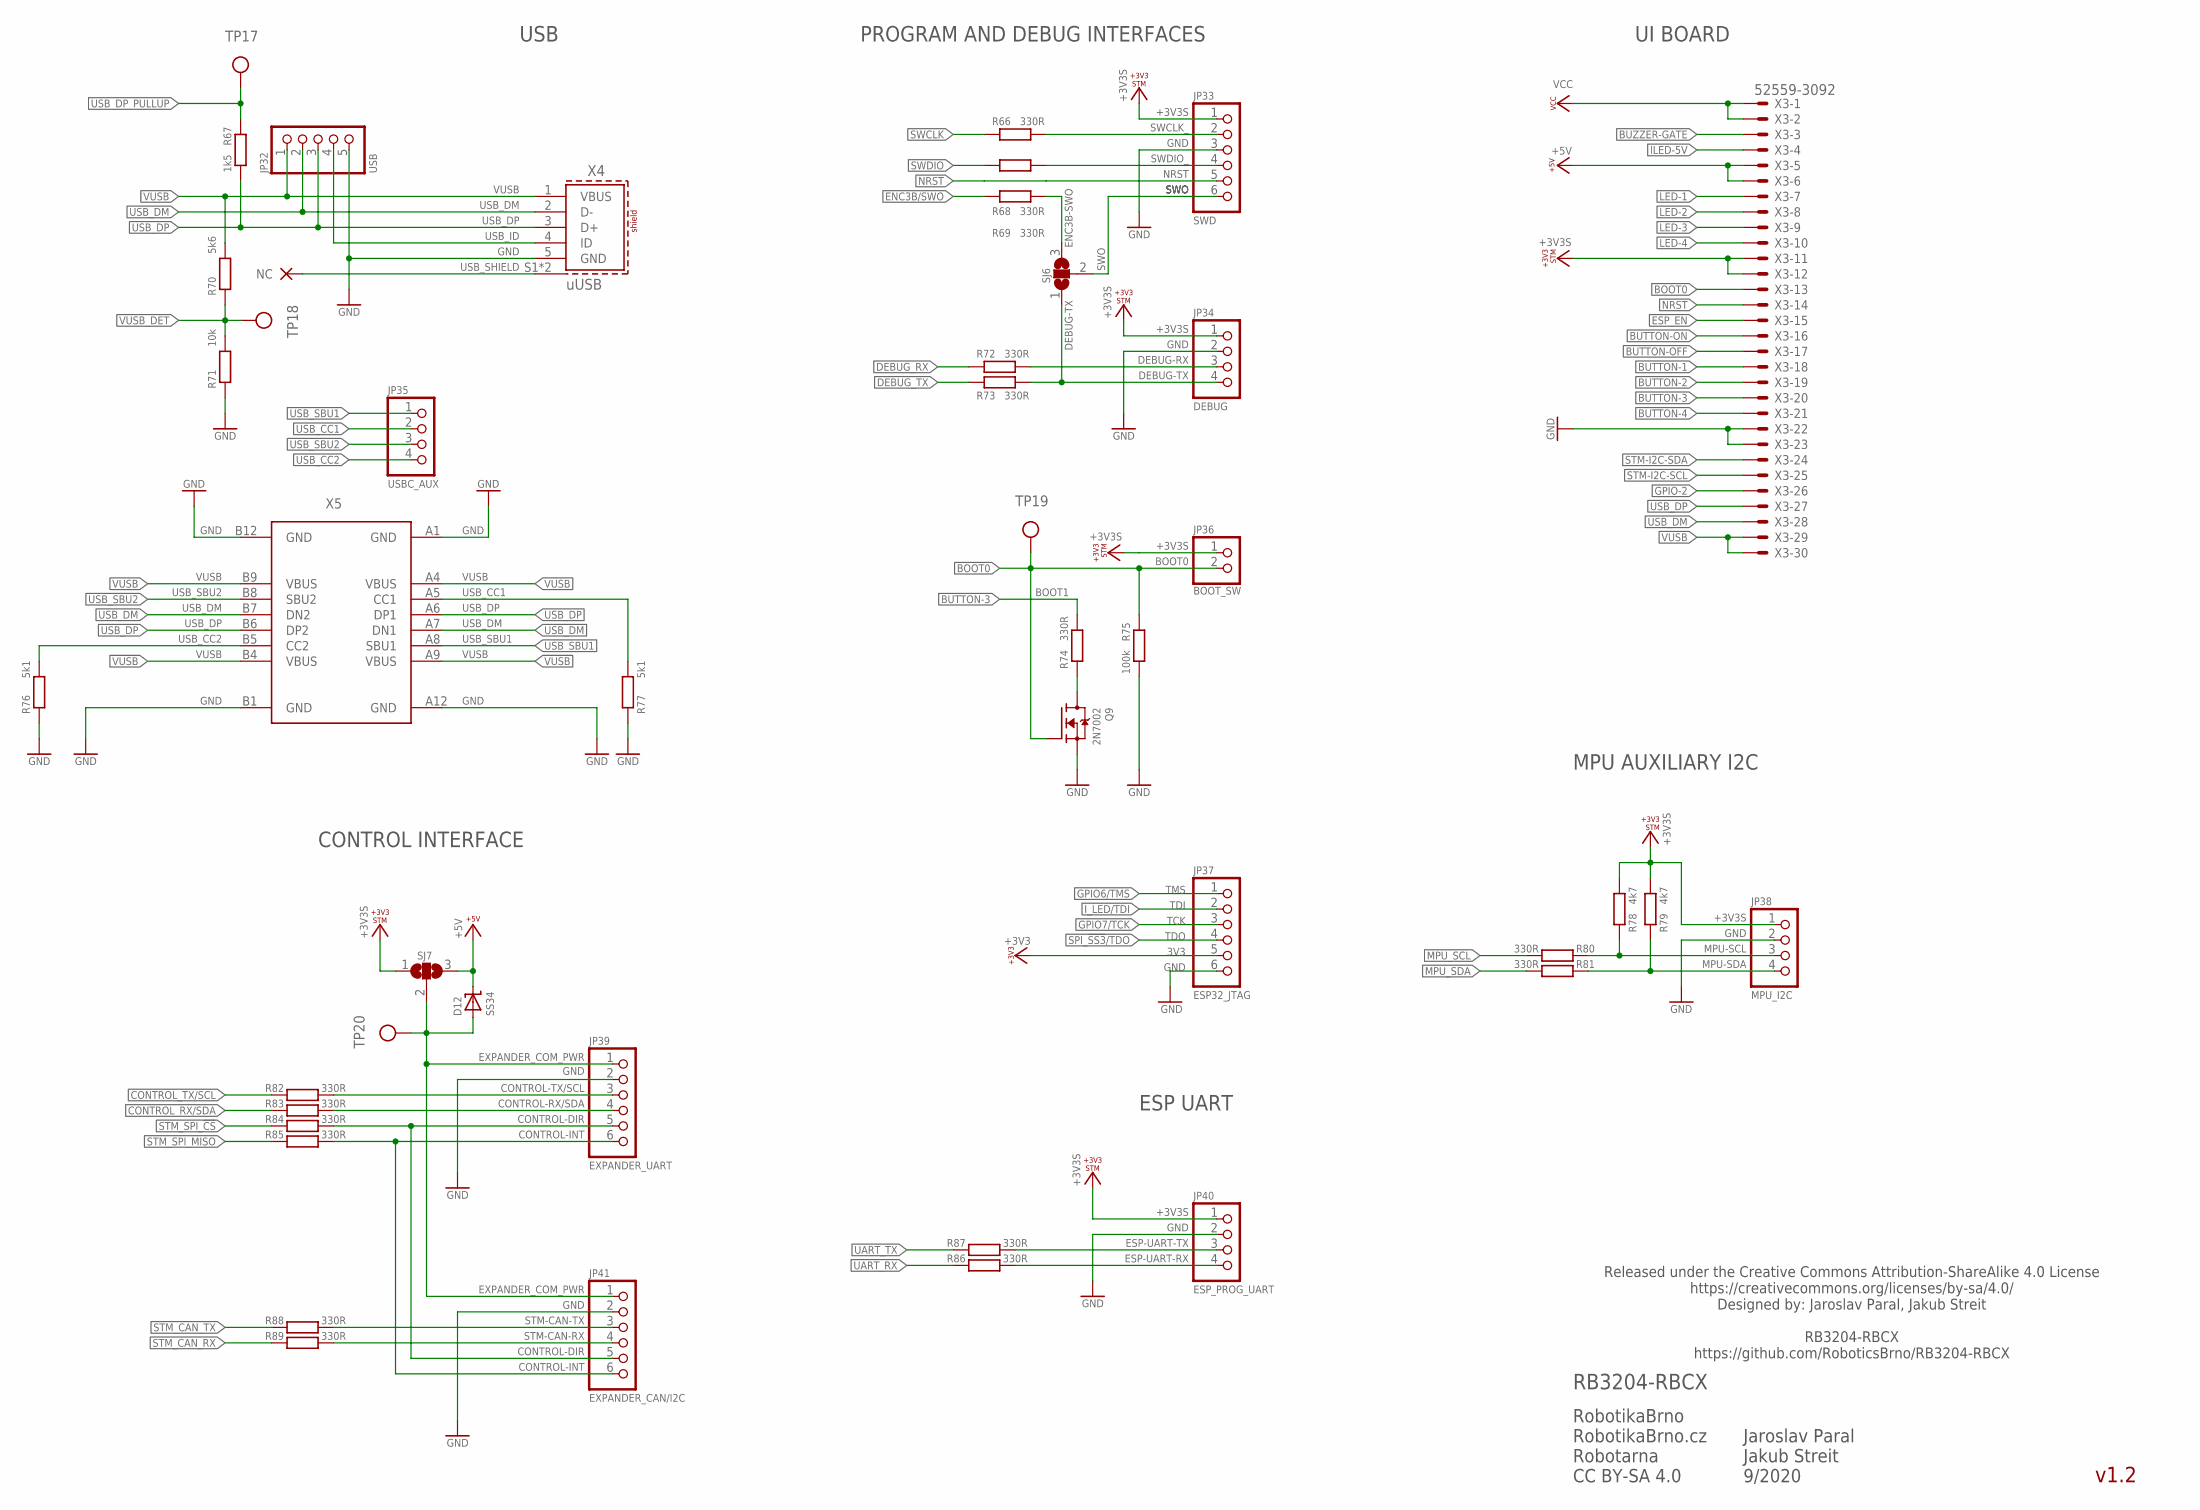
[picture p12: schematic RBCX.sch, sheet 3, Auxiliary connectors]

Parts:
D12: SS34; SMA
JP32: USB; 1X05
JP33: SWD; 1X06
JP34: DEBUG; 1X04
JP35: USBC_AUX; 1X04
JP36: BOOT_SW; 1X02
JP37: ESP32_JTAG; 1X06
JP38: MPU_I2C; 1X04
JP39: EXPANDER_UART; 1X06
JP40: ESP_PROG_UART; 1X04
JP41: EXPANDER_CAN/I2C; 1X06
Q9: 2N7002; SOT23; LCSC_ID C8545
R66, R68, R69, R72, R73, R74, R80, R81, R82, R83, R84, R85, R86, R87, R88, R89: 330R; R0402
R67: 1k5; R0402; LCSC_ID C25867
R70: 5k6; R0402
R71: 10k; R0402
R75: 100k; R0402
R76, R77: 5k1; R0402
R78, R79: 4k7; R0402
SJ6, SJ7: SJ2W0603; SJ_2_0603
TP17, TP18, TP19, TP20: TP_06MM; TP_06
X3: 52559-3092
X4: uUSB; 614105150621
X5: USB_C_8PIN; USB_C_VERT_THT_8PIN

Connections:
+3V3: JP37.5; also elsewhere on the board
+3V3S: JP33.1, JP34.1, JP36.1, JP38.1, JP40.1, R78.2, R79.2, SJ7.1, X3.11, X3.12; also elsewhere on the board
+5V: D12.C, SJ7.3, X3.5, X3.6; also elsewhere on the board
BOOT0: JP36.2, Q9.1 (G), R75.1, TP19.P$1, X3.13; also elsewhere on the board
BOOT1_PULL-DOWN: Q9.3 (D), R74.1
BUTTON-1: X3.18; also elsewhere on the board
BUTTON-2: X3.19; also elsewhere on the board
BUTTON-3: R74.2, X3.20; also elsewhere on the board
BUTTON-4: X3.21; also elsewhere on the board
BUTTON-OFF: X3.17; also elsewhere on the board
BUTTON-ON: X3.16; also elsewhere on the board
BUZZER-GATE: X3.3; also elsewhere on the board
CONTROL-DIR: JP39.5, JP41.5, R84.2
CONTROL-INT: JP39.6, JP41.6, R85.2
CONTROL-RX/SDA: JP39.4, R83.2
CONTROL-TX/SCL: JP39.3, R82.2
CONTROL_RX/SDA: R83.1; also elsewhere on the board
CONTROL_TX/SCL: R82.1; also elsewhere on the board
DEBUG-RX: JP34.3, R72.2
DEBUG-TX: JP34.4, R73.2, SJ6.1
DEBUG_RX: R72.1; also elsewhere on the board
DEBUG_TX: R73.1; also elsewhere on the board
ENC3B-SWO: R69.2, SJ6.3
ENC3B/SWO: R69.1; also elsewhere on the board
ESP-UART-RX: JP40.4, R87.2
ESP-UART-TX: JP40.3, R86.2
ESP_EN: X3.15; also elsewhere on the board
EXPANDER_COM_PWR: D12.A, JP39.1, JP41.1, SJ7.2, TP20.P$1
GND: JP32.5, JP33.3, JP34.2, JP37.6, JP38.2, JP39.2, JP40.2, JP41.2, Q9.2 (S), R71.1, R75.2, R76.2, R77.2, X3.22, X3.23, X4.5 (GND), X5.A1 (GND), X5.A12 (GND), X5.B1 (GND), X5.B12 (GND); also elsewhere on the board
GPIO6/TMS: JP37.1; also elsewhere on the board
GPIO7/TCK: JP37.3; also elsewhere on the board
GPIO-2: X3.26; also elsewhere on the board
ILED-5V: X3.4; also elsewhere on the board
I_LED/TDI: JP37.2; also elsewhere on the board
LED-1: X3.7; also elsewhere on the board
LED-2: X3.8; also elsewhere on the board
LED-3: X3.9; also elsewhere on the board
LED-4: X3.10; also elsewhere on the board
MPU-SCL: JP38.3, R78.1, R80.1
MPU-SDA: JP38.4, R79.1, R81.1
MPU_SCL: R80.2; also elsewhere on the board
MPU_SDA: R81.2; also elsewhere on the board
NRST: JP33.5, X3.14; also elsewhere on the board
SPI_!SS3!/TDO: JP37.4; also elsewhere on the board
STM-CAN-RX: JP41.4, R89.2
STM-CAN-TX: JP41.3, R88.2
STM-I2C-SCL: X3.25; also elsewhere on the board
STM-I2C-SDA: X3.24; also elsewhere on the board
STM_CAN_RX: R89.1; also elsewhere on the board
STM_CAN_TX: R88.1; also elsewhere on the board
STM_SPI_!CS: R84.1; also elsewhere on the board
STM_SPI_MISO: R85.1; also elsewhere on the board
SWCLK: R66.1; also elsewhere on the board
SWCLK_: JP33.2, R66.2
SWDIO: R68.1; also elsewhere on the board
SWDIO_: JP33.4, R68.2
SWO: JP33.6, SJ6.2
UART_RX: R87.1; also elsewhere on the board
UART_TX: R86.1; also elsewhere on the board
USB_CC1: JP35.2, R77.1, X5.A5 (CC1)
USB_CC2: JP35.4, R76.1, X5.B5 (CC2)
USB_DM: JP32.2, X3.28, X4.2 (D-), X5.A7 (DN1), X5.B7 (DN2); also elsewhere on the board
USB_DP: JP32.3, R67.2, X3.27, X4.3 (D+), X5.A6 (DP1), X5.B6 (DP2); also elsewhere on the board
USB_DP_PULLUP: R67.1, TP17.P$1; also elsewhere on the board
USB_ID: JP32.4, X4.4 (ID)
USB_SBU1: JP35.1, X5.A8 (SBU1)
USB_SBU2: JP35.3, X5.B8 (SBU2)
USB_SHIELD: X4.S1 (SHIELD), X4.S2 (SHIELD)
VCC: X3.1, X3.2; also elsewhere on the board
VUSB: JP32.1, R70.2, X3.29, X3.30, X4.1 (VBUS), X5.A4 (VBUS), X5.A9 (VBUS), X5.B4 (VBUS), X5.B9 (VBUS); also elsewhere on the board
VUSB_DET: R70.1, R71.2, TP18.P$1; also elsewhere on the board

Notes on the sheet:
v1.2
RobotikaBrno RobotikaBrno.cz Robotarna CC BY-SA 4.0
RB3204-RBCX
Released under the Creative Commons Attribution-ShareAlike 4.0 License https://creativecommons.org/licenses/by-sa/4.0/ Designed by: Jaroslav Paral, Jakub Streit RB3204-RBCX https://github.com/RoboticsBrno/RB3204-RBCX
Jaroslav Paral Jakub Streit 9/2020
PROGRAM AND DEBUG INTERFACES
USB
ESP UART
UI BOARD
TDI
TMS
TCK
TDO
3V3
GND
BOOT1
CONTROL INTERFACE
MPU AUXILIARY I2C

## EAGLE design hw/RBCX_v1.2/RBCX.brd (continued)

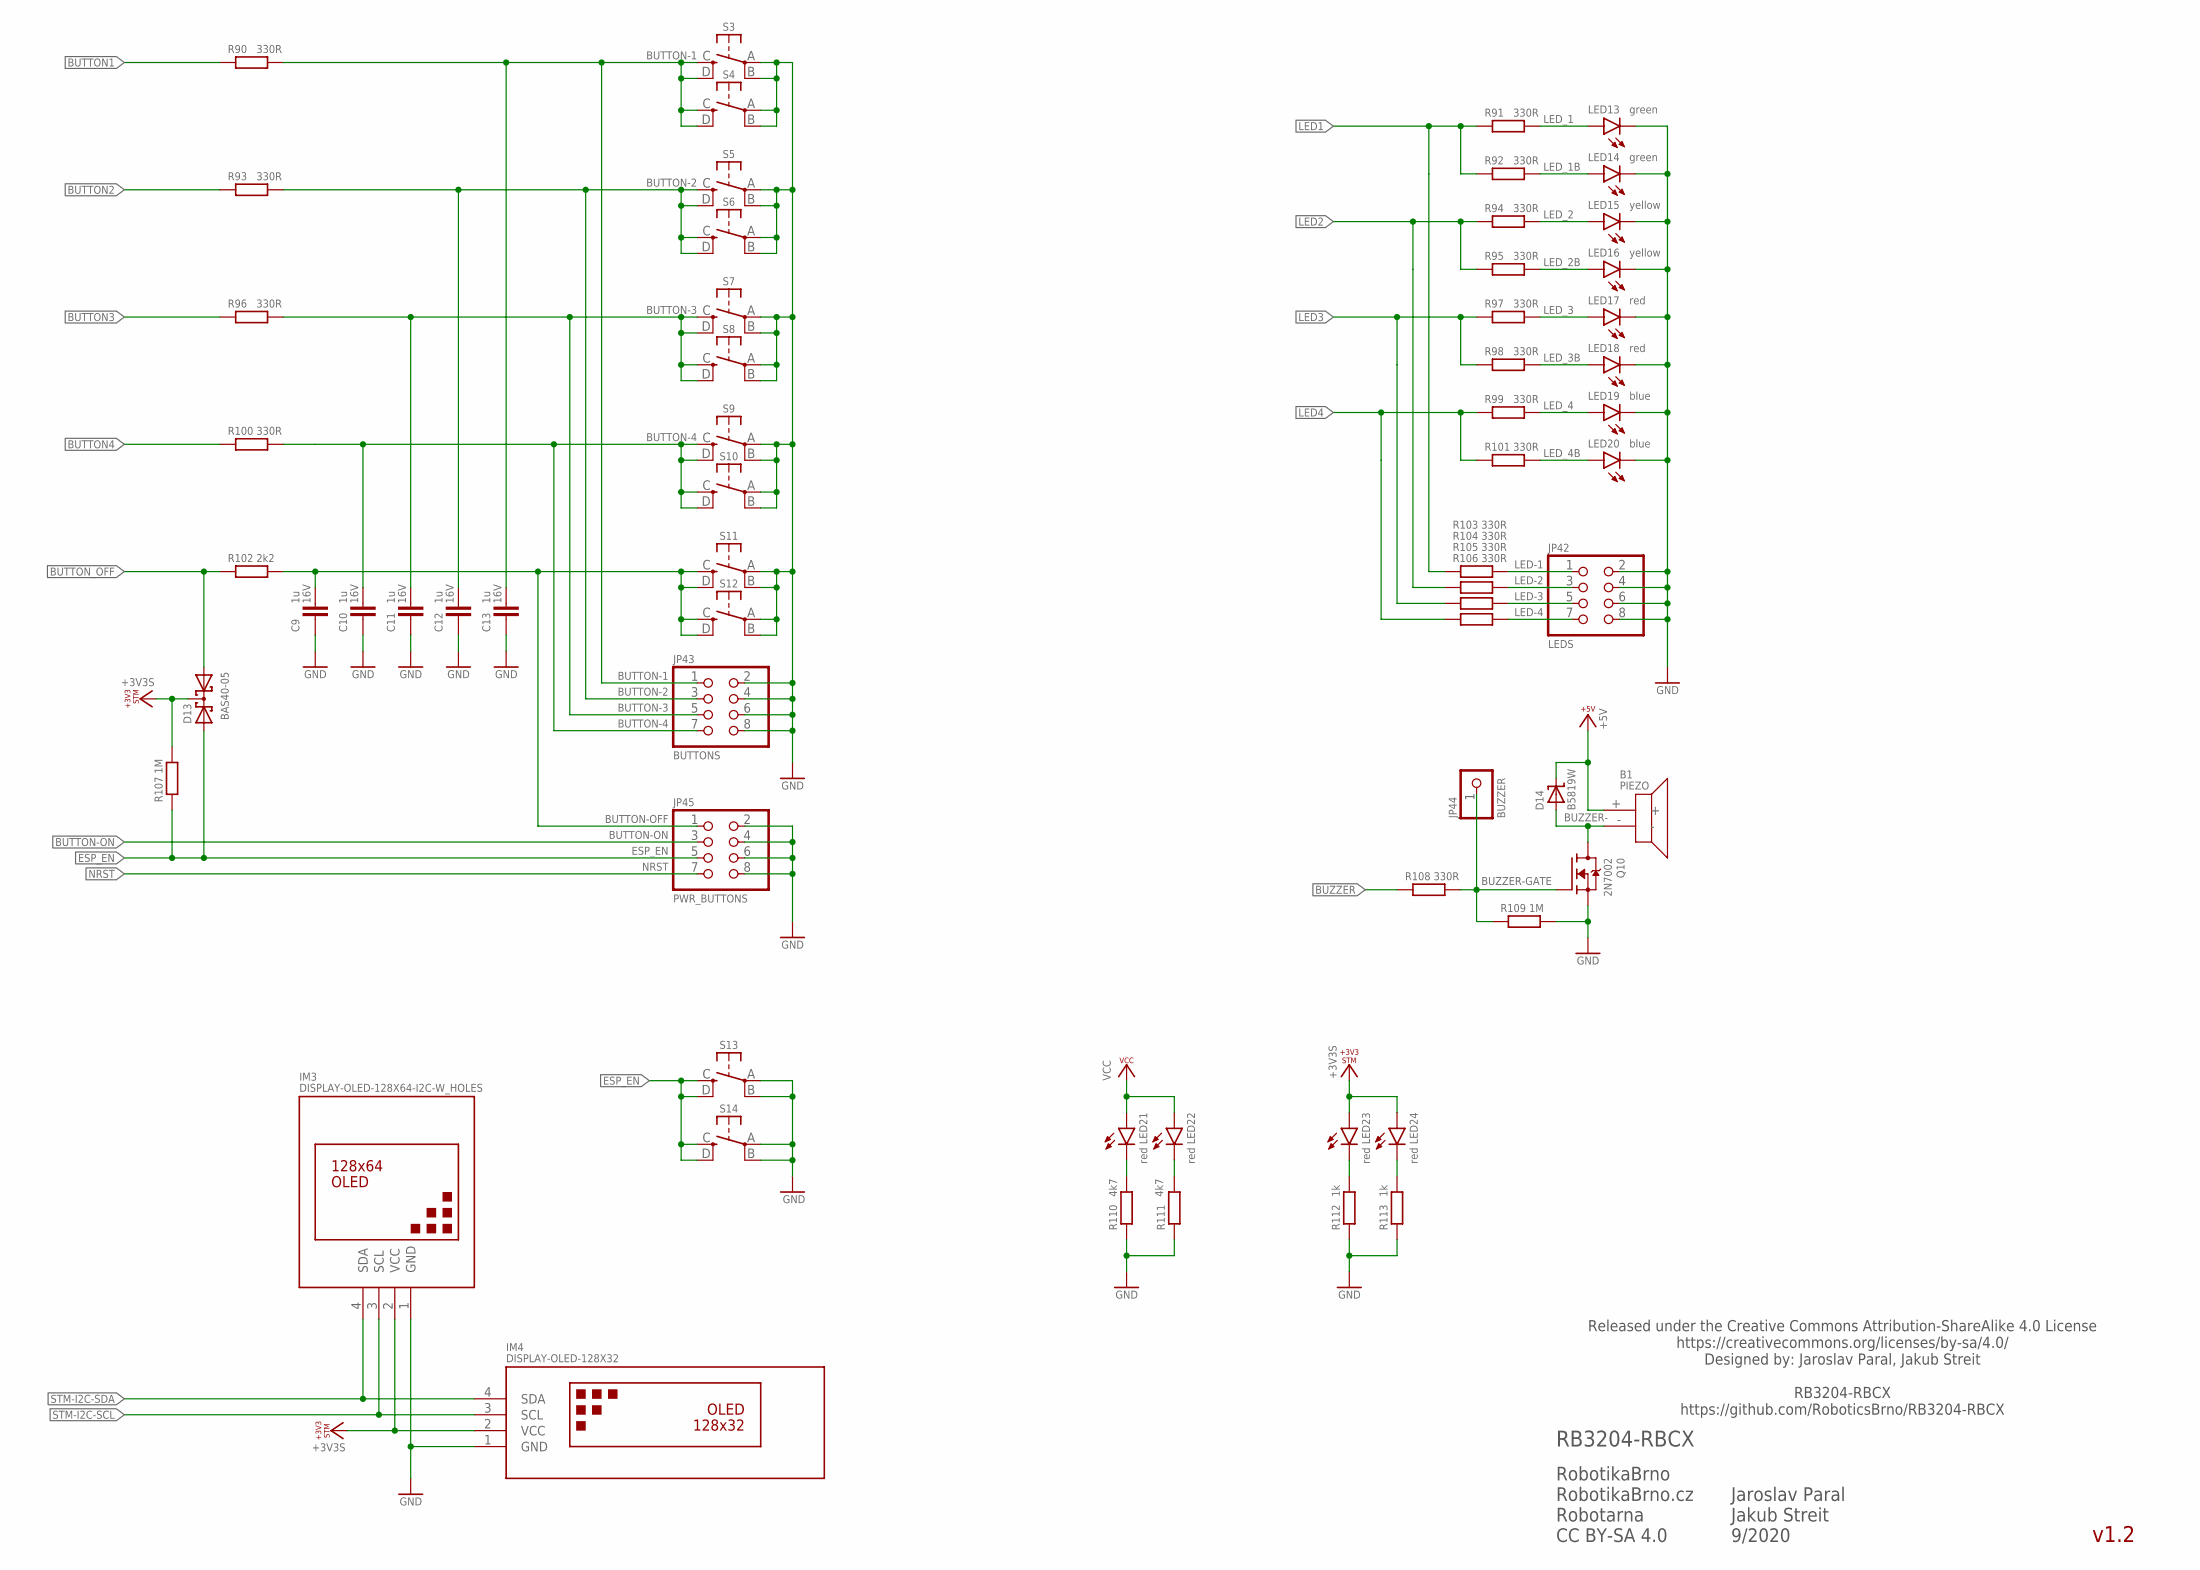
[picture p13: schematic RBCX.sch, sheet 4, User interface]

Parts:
B1: PIEZO
C9, C10, C11, C12, C13: 1u; C0402; VOLTAGE 16V
D13: BAS40-05; SOT23
D14: B5819W; SOD123; LCSC_ID C305445
IM3: DISPLAY-OLED-128X64-I2C-W_HOLES; DISPLAY-OLED-128X64-I2C_W-HOLES
IM4: DISPLAY-OLED-128X32
JP42: LEDS; 2X04
JP43: BUTTONS; 2X04
JP44: BUZZER; 1X01
JP45: PWR_BUTTONS; 2X04
LED13, LED14: green; CHIPLED_0603
LED15, LED16: yellow; CHIPLED_0603
LED17, LED18, LED21, LED22, LED23, LED24: red; CHIPLED_0603
LED19, LED20: blue; CHIPLED_0603
Q10: 2N7002; SOT23; LCSC_ID C8545
R90, R91, R92, R93, R94, R95, R96, R97, R98, R99, R100, R101, R103, R104, R105, R106, R108: 330R; R0402
R102: 2k2; R0402
R107, R109: 1M; R0402
R110, R111: 4k7; R0402
R112, R113: 1k; R0402
S3, S4, S5, S6, S7, S8, S9, S10, S11, S12, S13, S14: TS-1187A-C-C-B; TS-1187A

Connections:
+3V3S: D13.3 (C), IM3.2 (VCC), IM4.2 (VCC), LED23.A, LED24.A, R107.2; also elsewhere on the board
+5V: B1.+, D14.C; also elsewhere on the board
BUTTON1: R90.1; also elsewhere on the board
BUTTON2: R93.1; also elsewhere on the board
BUTTON3: R96.1; also elsewhere on the board
BUTTON4: R100.1; also elsewhere on the board
BUTTON-1: C13.1, JP43.1, R90.2, S3.C (S), S3.D (S1), S4.C (S), S4.D (S1); also elsewhere on the board
BUTTON-2: C12.1, JP43.3, R93.2, S5.C (S), S5.D (S1), S6.C (S), S6.D (S1); also elsewhere on the board
BUTTON-3: C11.1, JP43.5, R96.2, S7.C (S), S7.D (S1), S8.C (S), S8.D (S1); also elsewhere on the board
BUTTON-4: C10.1, JP43.7, R100.2, S9.C (S), S9.D (S1), S10.C (S), S10.D (S1); also elsewhere on the board
BUTTON-OFF: C9.1, JP45.1, R102.2, S11.C (S), S11.D (S1), S12.C (S), S12.D (S1); also elsewhere on the board
BUTTON-ON: JP45.3; also elsewhere on the board
BUTTON_OFF: D13.1 (A1), R102.1; also elsewhere on the board
BUZZER: R108.1; also elsewhere on the board
BUZZER-: B1.-, D14.A, Q10.3 (D)
BUZZER-GATE: JP44.1, Q10.1 (G), R108.2, R109.1; also elsewhere on the board
ESP_EN: D13.2 (A2), JP45.5, R107.1, S13.C (S), S13.D (S1), S14.C (S), S14.D (S1); also elsewhere on the board
GND: C9.2, C10.2, C11.2, C12.2, C13.2, IM3.1 (GND), IM4.1 (GND), JP42.2, JP42.4, JP42.6, JP42.8, JP43.2, JP43.4, JP43.6, JP43.8, JP45.2, JP45.4, JP45.6, JP45.8, LED13.C, LED14.C, LED15.C, LED16.C, LED17.C, LED18.C, LED19.C, LED20.C, Q10.2 (S), R109.2, R110.1, R111.1, R112.1, R113.1, S3.A, S3.B (P1), S4.A, S4.B (P1), S5.A, S5.B (P1), S6.A, S6.B (P1), S7.A, S7.B (P1), S8.A, S8.B (P1), S9.A, S9.B (P1), S10.A, S10.B (P1), S11.A, S11.B (P1), S12.A, S12.B (P1), S13.A, S13.B (P1), S14.A, S14.B (P1); also elsewhere on the board
LED1: R91.1, R92.1, R103.1; also elsewhere on the board
LED2: R94.1, R95.1, R104.1; also elsewhere on the board
LED3: R97.1, R98.1, R105.1; also elsewhere on the board
LED4: R99.1, R101.1, R106.1; also elsewhere on the board
LED-1: JP42.1, R103.2; also elsewhere on the board
LED-2: JP42.3, R104.2; also elsewhere on the board
LED-3: JP42.5, R105.2; also elsewhere on the board
LED-4: JP42.7, R106.2; also elsewhere on the board
LED_1: LED13.A, R91.2
LED_1B: LED14.A, R92.2
LED_2: LED15.A, R94.2
LED_2B: LED16.A, R95.2
LED_3: LED17.A, R97.2
LED_3B: LED18.A, R98.2
LED_4: LED19.A, R99.2
LED_4B: LED20.A, R101.2
NRST: JP45.7; also elsewhere on the board
PWRLED_+3V3S1: LED23.C, R112.2
PWRLED_+3V3S_B1: LED24.C, R113.2
PWRLED_VCC1: LED21.C, R110.2
PWRLED_VCC_B1: LED22.C, R111.2
STM-I2C-SCL: IM3.3 (SCL), IM4.3 (SCL); also elsewhere on the board
STM-I2C-SDA: IM3.4 (SDA), IM4.4 (SDA); also elsewhere on the board
VCC: LED21.A, LED22.A; also elsewhere on the board

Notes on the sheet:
v1.2
RobotikaBrno RobotikaBrno.cz Robotarna CC BY-SA 4.0
RB3204-RBCX
Released under the Creative Commons Attribution-ShareAlike 4.0 License https://creativecommons.org/licenses/by-sa/4.0/ Designed by: Jaroslav Paral, Jakub Streit RB3204-RBCX https://github.com/RoboticsBrno/RB3204-RBCX
Jaroslav Paral Jakub Streit 9/2020

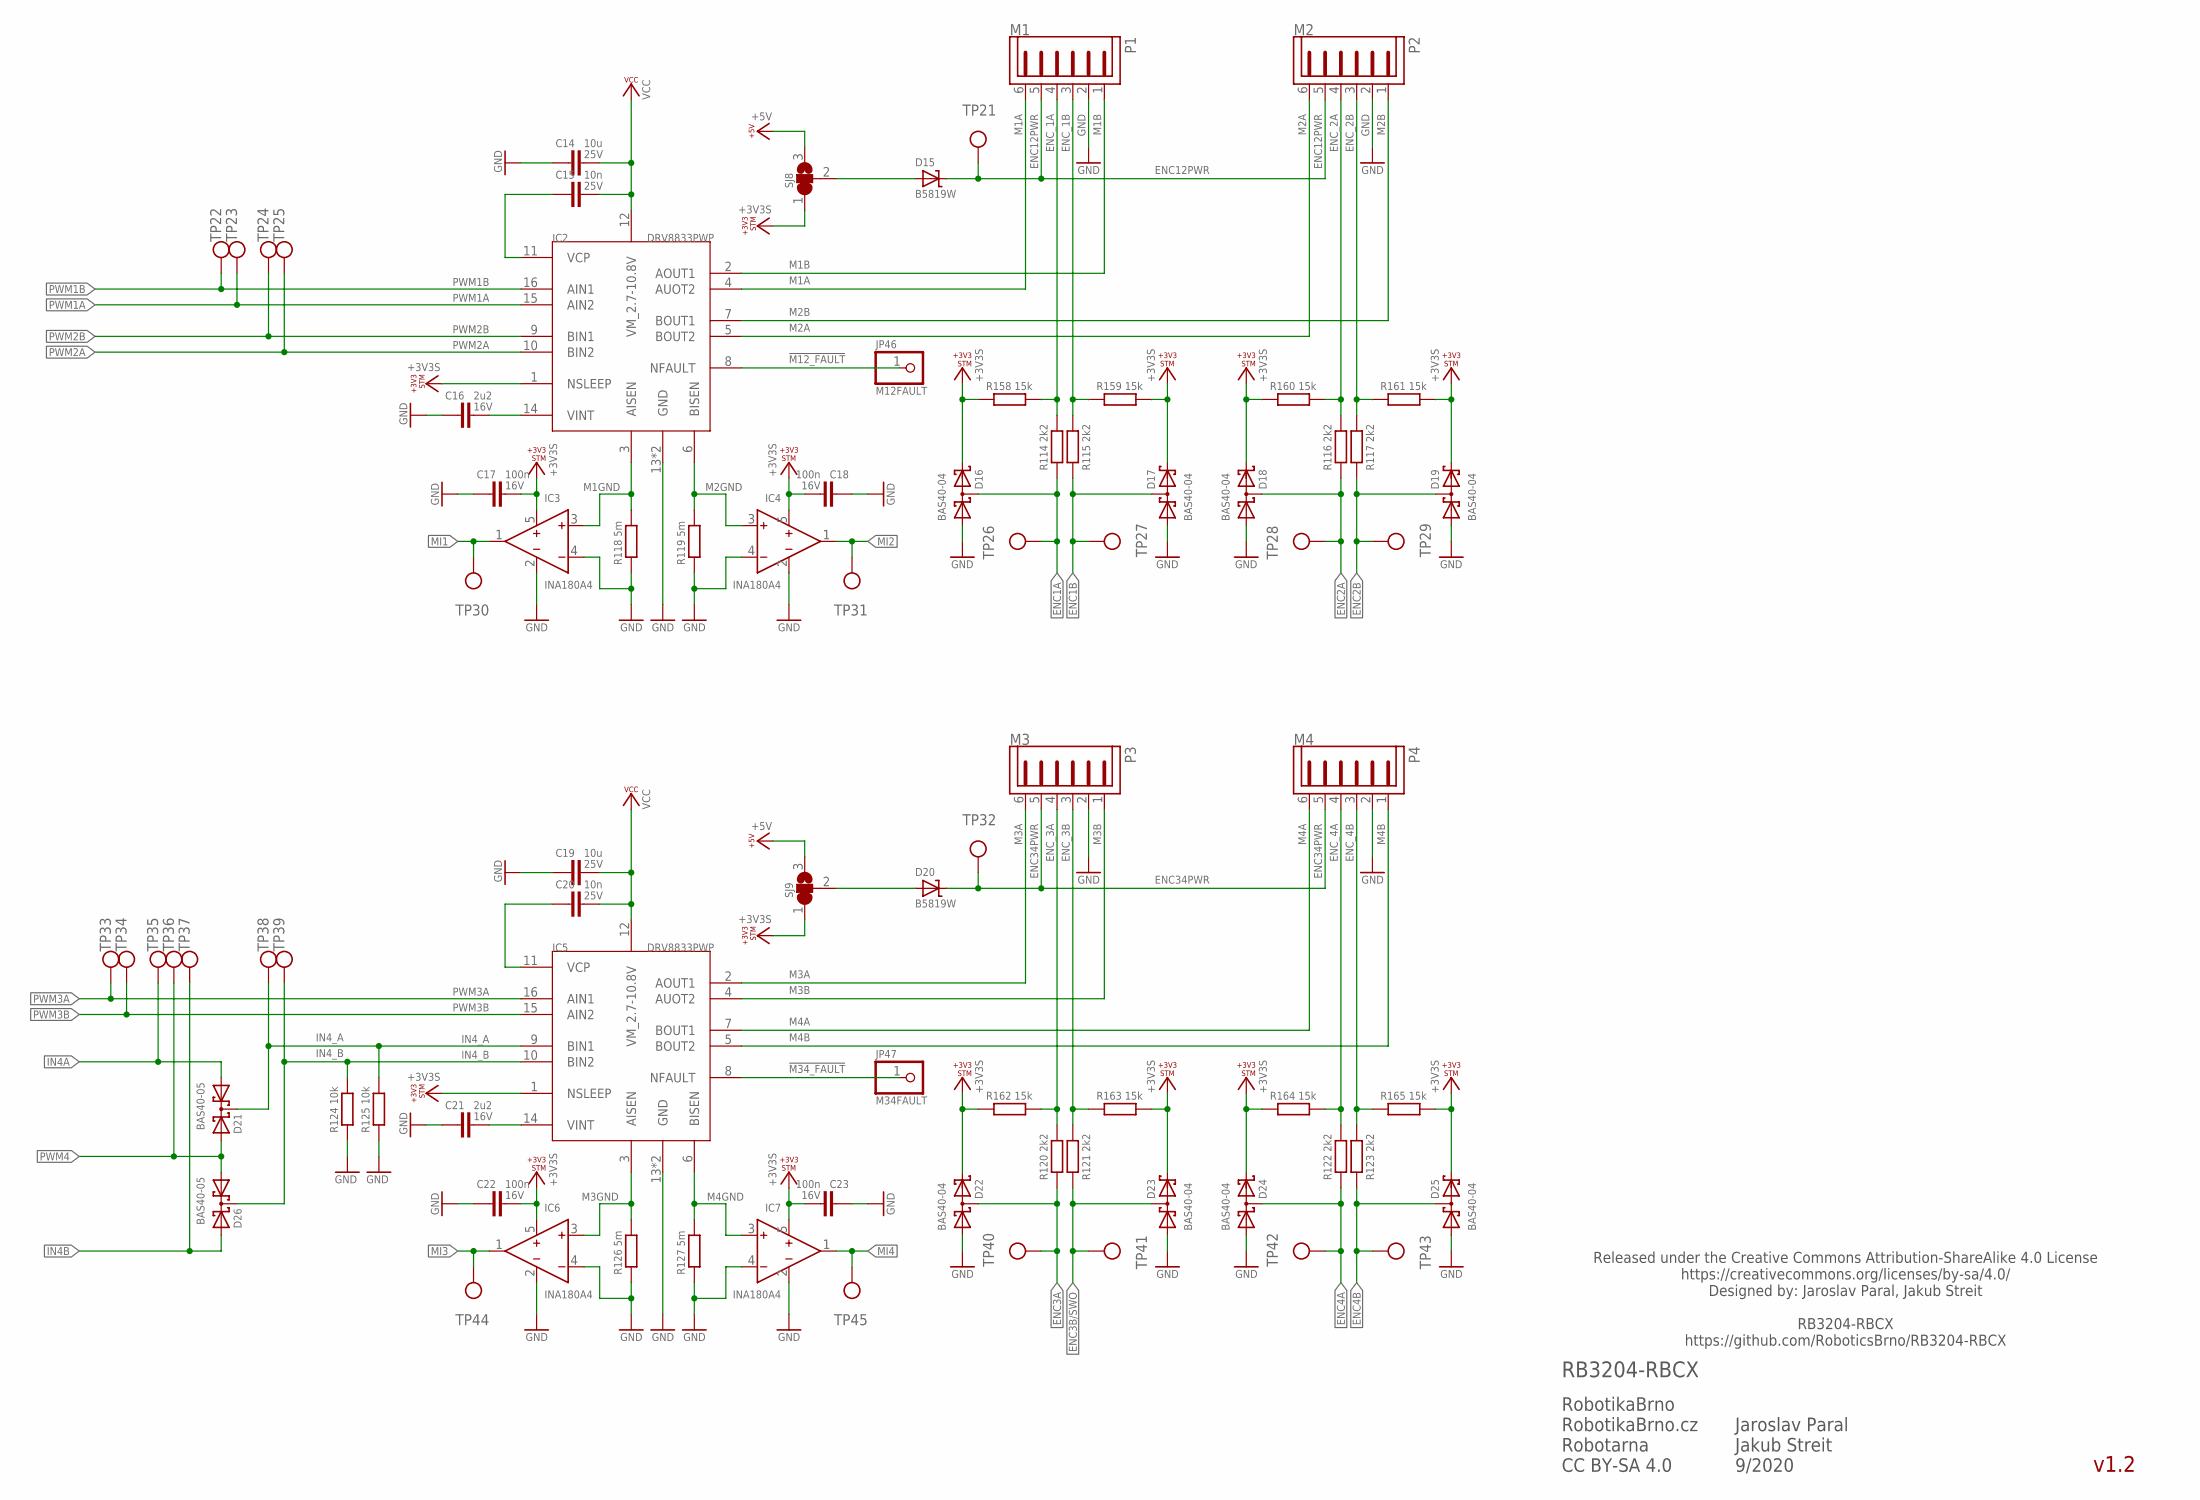
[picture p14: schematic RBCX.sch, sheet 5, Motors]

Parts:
C14, C19: 10u; C0805; VOLTAGE 25V
C15, C20: 10n; C0402; VOLTAGE 25V
C16, C21: 2u2; C0603; VOLTAGE 16V
C17, C18, C22, C23: 100n; C0402; VOLTAGE 16V
D15, D20: B5819W; SOD123; LCSC_ID C305445
D16, D17, D18, D19, D22, D23, D24, D25: BAS40-04; SOT23
D21, D26: BAS40-05; SOT23
IC2, IC5: DRV8833PWP; HTSSOP
IC3, IC4, IC6, IC7: INA180A4; SOT23-5L; LCSC_ID C133969
JP46: M12FAULT; 1X01
JP47: M34FAULT; 1X01
P1: M1; JST-PH6
P2: M2; JST-PH6
P3: M3; JST-PH6
P4: M4; JST-PH6
R114, R115, R116, R117, R120, R121, R122, R123: 2k2; R0402
R118, R119, R126, R127: 5m; R1206
R124, R125: 10k; R0402
R158, R159, R160, R161, R162, R163, R164, R165: 15k; R0402
SJ8, SJ9: SJ2W_DEFAULT; SJ_2_DEFAULT
TP21, TP22, TP23, TP24, TP25, TP26, TP27, TP28, TP29, TP30, TP31, TP32, TP33, TP34, TP35, TP36, TP37, TP38, TP39, TP40, TP41, TP42, TP43, TP44, TP45: TP_06MM; TP_06

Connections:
!M12_FAULT: IC2.8 (NFAULT), JP46.1
!M34_FAULT: IC5.8 (NFAULT), JP47.1
+3V3S: C17.1, C18.1, C22.1, C23.1, D16.2 (C2), D17.2 (C2), D18.2 (C2), D19.2 (C2), D22.2 (C2), D23.2 (C2), D24.2 (C2), D25.2 (C2), IC2.1 (NSLEEP), IC3.5 (VCC), IC4.5 (VCC), IC5.1 (NSLEEP), IC6.5 (VCC), IC7.5 (VCC), R158.1, R159.2, R160.1, R161.2, R162.1, R163.2, R164.1, R165.2, SJ8.1, SJ9.1; also elsewhere on the board
+5V: SJ8.3, SJ9.3; also elsewhere on the board
ENC1A: D16.3 (C1A2), R114.1, TP26.P$1; also elsewhere on the board
ENC1B: D17.3 (C1A2), R115.1, TP27.P$1; also elsewhere on the board
ENC2A: D18.3 (C1A2), R116.1, TP28.P$1; also elsewhere on the board
ENC2B: D19.3 (C1A2), R117.1, TP29.P$1; also elsewhere on the board
ENC3A: D22.3 (C1A2), R120.1, TP40.P$1; also elsewhere on the board
ENC3B/SWO: D23.3 (C1A2), R121.1, TP41.P$1; also elsewhere on the board
ENC4A: D24.3 (C1A2), R122.1, TP42.P$1; also elsewhere on the board
ENC4B: D25.3 (C1A2), R123.1, TP43.P$1; also elsewhere on the board
ENC12PWR: D15.C, P1.5, P2.5, TP21.P$1
ENC12_PWR: D15.A, SJ8.2
ENC34PWR: D20.C, P3.5, P4.5, TP32.P$1
ENC34_PWR: D20.A, SJ9.2
ENC_1A: P1.4, R114.2, R158.2
ENC_1B: P1.3, R115.2, R159.1
ENC_2A: P2.4, R116.2, R160.2
ENC_2B: P2.3, R117.2, R161.1
ENC_3A: P3.4, R120.2, R162.2
ENC_3B: P3.3, R121.2, R163.1
ENC_4A: P4.4, R122.2, R164.2
ENC_4B: P4.3, R123.2, R165.1
GND: C14.2, C16.2, C17.2, C18.2, C19.2, C21.2, C22.2, C23.2, D16.1 (A1), D17.1 (A1), D18.1 (A1), D19.1 (A1), D22.1 (A1), D23.1 (A1), D24.1 (A1), D25.1 (A1), IC2.13 (GND), IC2.GND, IC3.2 (GND), IC3.4 (IN-), IC4.2 (GND), IC4.4 (IN-), IC5.13 (GND), IC5.GND, IC6.2 (GND), IC6.4 (IN-), IC7.2 (GND), IC7.4 (IN-), P1.2, P2.2, P3.2, P4.2, R118.1, R119.1, R124.1, R125.1, R126.1, R127.1; also elsewhere on the board
IN4A: D21.1 (A1), TP35.P$1; also elsewhere on the board
IN4B: D26.2 (A2), TP37.P$1; also elsewhere on the board
IN4_A: D21.3 (C), IC5.9 (BIN1), R125.2, TP38.P$1
IN4_B: D26.3 (C), IC5.10 (BIN2), R124.2, TP39.P$1
M1A: IC2.4 (AUOT2), P1.6
M1B: IC2.2 (AOUT1), P1.1
M1GND: IC2.3 (AISEN), IC3.3 (IN+), R118.2
M2A: IC2.5 (BOUT2), P2.6
M2B: IC2.7 (BOUT1), P2.1
M2GND: IC2.6 (BISEN), IC4.3 (IN+), R119.2
M3A: IC5.2 (AOUT1), P3.6
M3B: IC5.4 (AUOT2), P3.1
M3GND: IC5.3 (AISEN), IC6.3 (IN+), R126.2
M4A: IC5.7 (BOUT1), P4.6
M4B: IC5.5 (BOUT2), P4.1
M4GND: IC5.6 (BISEN), IC7.3 (IN+), R127.2
MI1: IC3.1 (OUT), TP30.P$1; also elsewhere on the board
MI2: IC4.1 (OUT), TP31.P$1; also elsewhere on the board
MI3: IC6.1 (OUT), TP44.P$1; also elsewhere on the board
MI4: IC7.1 (OUT), TP45.P$1; also elsewhere on the board
PWM1A: IC2.15 (AIN2), TP23.P$1; also elsewhere on the board
PWM1B: IC2.16 (AIN1), TP22.P$1; also elsewhere on the board
PWM2A: IC2.10 (BIN2), TP25.P$1; also elsewhere on the board
PWM2B: IC2.9 (BIN1), TP24.P$1; also elsewhere on the board
PWM3A: IC5.16 (AIN1), TP33.P$1; also elsewhere on the board
PWM3B: IC5.15 (AIN2), TP34.P$1; also elsewhere on the board
PWM4: D21.2 (A2), D26.1 (A1), TP36.P$1; also elsewhere on the board
VCC: C14.1, C15.1, C19.1, C20.1, IC2.12 (VM_2.7-10.8V), IC5.12 (VM_2.7-10.8V); also elsewhere on the board
VCP12: C15.2, IC2.11 (VCP)
VCP34: C20.2, IC5.11 (VCP)
VINT12: C16.1, IC2.14 (VINT)
VINT34: C21.1, IC5.14 (VINT)

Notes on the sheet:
v1.2
RobotikaBrno RobotikaBrno.cz Robotarna CC BY-SA 4.0
RB3204-RBCX
Released under the Creative Commons Attribution-ShareAlike 4.0 License https://creativecommons.org/licenses/by-sa/4.0/ Designed by: Jaroslav Paral, Jakub Streit RB3204-RBCX https://github.com/RoboticsBrno/RB3204-RBCX
Jaroslav Paral Jakub Streit 9/2020

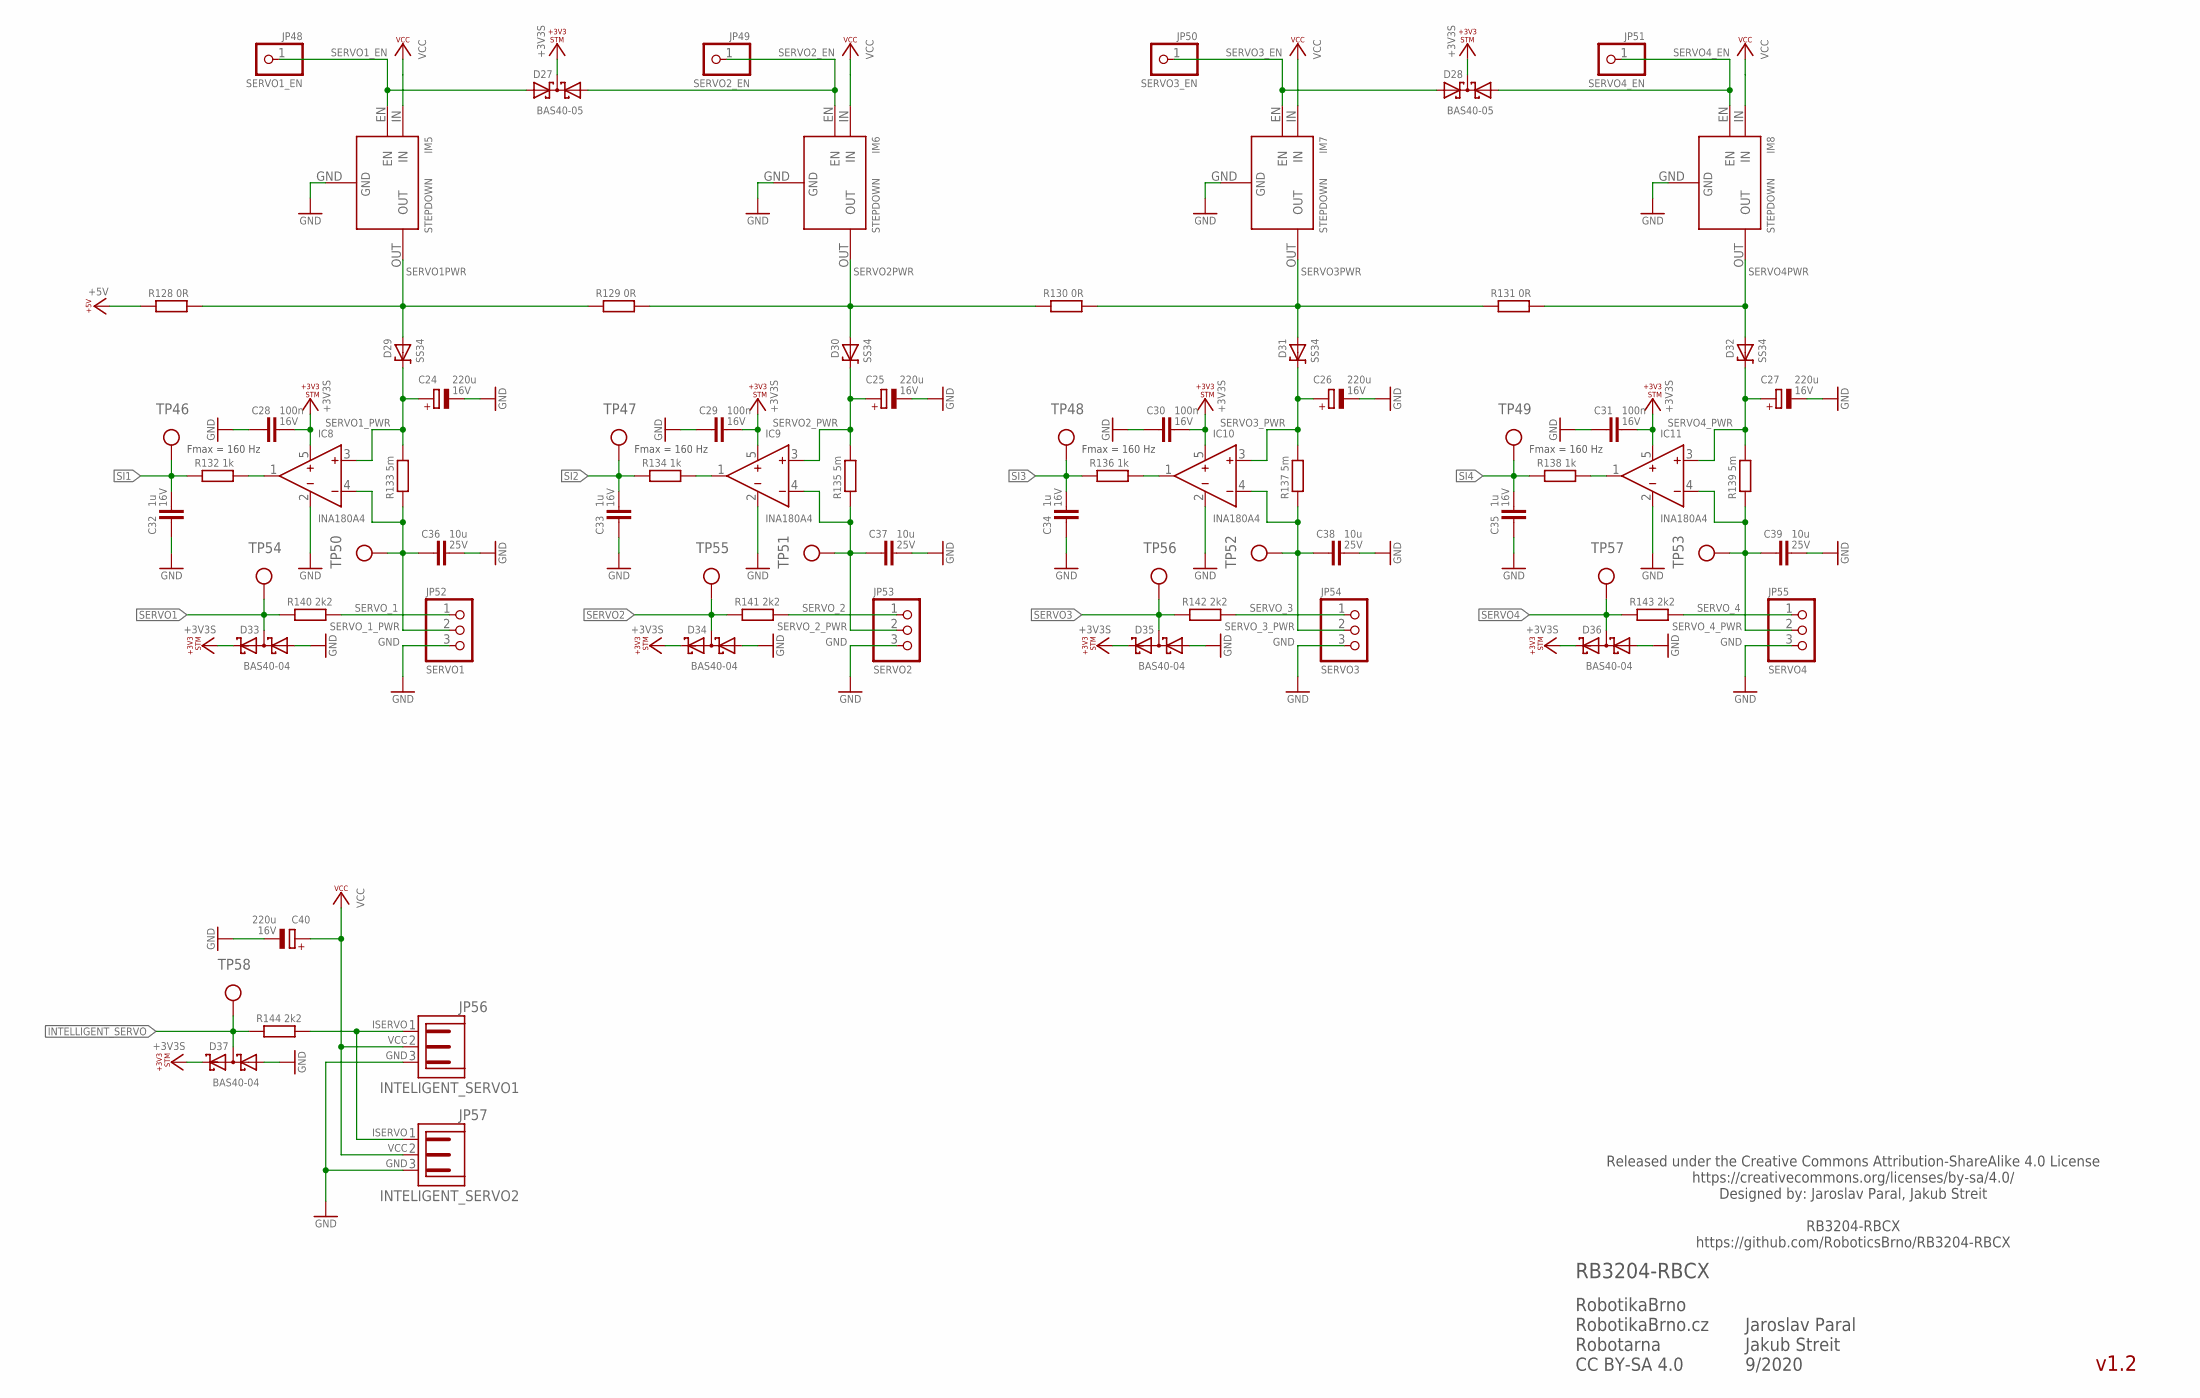
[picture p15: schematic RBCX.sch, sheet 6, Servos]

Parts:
C24, C25, C26, C27, C40: 220u; E5-10,5; VOLTAGE 16V
C28, C29, C30, C31: 100n; C0402; VOLTAGE 16V
C32, C33, C34, C35: 1u; C0402; VOLTAGE 16V
C36, C37, C38, C39: 10u; C0805; VOLTAGE 25V
D27, D28: BAS40-05; SOT23
D29, D30, D31, D32: SS34; SMA
D33, D34, D35, D36, D37: BAS40-04; SOT23
IC8, IC9, IC10, IC11: INA180A4; SOT23-5L; LCSC_ID C133969
IM5, IM6, IM7, IM8: STEPDOWN
JP48: SERVO1_EN; 1X01
JP49: SERVO2_EN; 1X01
JP50: SERVO3_EN; 1X01
JP51: SERVO4_EN; 1X01
JP52: SERVO1; 1X03
JP53: SERVO2; 1X03
JP54: SERVO3; 1X03
JP55: SERVO4; 1X03
JP56: INTELIGENT_SERVO1; JST-PH3
JP57: INTELIGENT_SERVO2; JST-PH3
R128, R129, R130, R131: 0R; R1206
R132, R134, R136, R138: 1k; R0402
R133, R135, R137, R139: 5m; R1206
R140, R141, R142, R143, R144: 2k2; R0402
TP46, TP47, TP48, TP49, TP50, TP51, TP52, TP53, TP54, TP55, TP56, TP57, TP58: TP_06MM; TP_06

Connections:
+3V3S: C28.1, C29.1, C30.1, C31.1, D27.3 (C), D28.3 (C), D33.2 (C2), D34.2 (C2), D35.2 (C2), D36.2 (C2), D37.2 (C2), IC8.5 (VCC), IC9.5 (VCC), IC10.5 (VCC), IC11.5 (VCC); also elsewhere on the board
+5V: R128.1; also elsewhere on the board
GND: C24.-, C25.-, C26.-, C27.-, C28.2, C29.2, C30.2, C31.2, C32.2, C33.2, C34.2, C35.2, C36.1, C37.1, C38.1, C39.1, C40.-, D33.1 (A1), D34.1 (A1), D35.1 (A1), D36.1 (A1), D37.1 (A1), IC8.2 (GND), IC9.2 (GND), IC10.2 (GND), IC11.2 (GND), IM5.GND, IM6.GND, IM7.GND, IM8.GND, JP52.3, JP53.3, JP54.3, JP55.3, JP56.3, JP57.3; also elsewhere on the board
INTELLIGENT_SERVO: D37.3 (C1A2), R144.1, TP58.P$1; also elsewhere on the board
ISERVO: JP56.1, JP57.1, R144.2
SERVO1: D33.3 (C1A2), R140.1, TP54.P$1; also elsewhere on the board
SERVO1PWR: D29.A, IM5.OUT, R128.2, R129.1
SERVO1_EN: D27.2 (A2), IM5.EN, JP48.1
SERVO1_PWR: C24.+, D29.C, IC8.3 (IN+), R133.2
SERVO2: D34.3 (C1A2), R141.1, TP55.P$1; also elsewhere on the board
SERVO2PWR: D30.A, IM6.OUT, R129.2, R130.1
SERVO2_EN: D27.1 (A1), IM6.EN, JP49.1
SERVO2_PWR: C25.+, D30.C, IC9.3 (IN+), R135.2
SERVO3: D35.3 (C1A2), R142.1, TP56.P$1; also elsewhere on the board
SERVO3PWR: D31.A, IM7.OUT, R130.2, R131.1
SERVO3_EN: D28.2 (A2), IM7.EN, JP50.1
SERVO3_PWR: C26.+, D31.C, IC10.3 (IN+), R137.2
SERVO4: D36.3 (C1A2), R143.1, TP57.P$1; also elsewhere on the board
SERVO4PWR: D32.A, IM8.OUT, R131.2
SERVO4_EN: D28.1 (A1), IM8.EN, JP51.1
SERVO4_PWR: C27.+, D32.C, IC11.3 (IN+), R139.2
SERVO_1: JP52.1, R140.2
SERVO_1_PWR: C36.2, IC8.4 (IN-), JP52.2, R133.1, TP50.P$1
SERVO_2: JP53.1, R141.2
SERVO_2_PWR: C37.2, IC9.4 (IN-), JP53.2, R135.1, TP51.P$1
SERVO_3: JP54.1, R142.2
SERVO_3_PWR: C38.2, IC10.4 (IN-), JP54.2, R137.1, TP52.P$1
SERVO_4: JP55.1, R143.2
SERVO_4_PWR: C39.2, IC11.4 (IN-), JP55.2, R139.1, TP53.P$1
SI1: C32.1, R132.1, TP46.P$1; also elsewhere on the board
SI2: C33.1, R134.1, TP47.P$1; also elsewhere on the board
SI3: C34.1, R136.1, TP48.P$1; also elsewhere on the board
SI4: C35.1, R138.1, TP49.P$1; also elsewhere on the board
SI_1: IC8.1 (OUT), R132.2
SI_2: IC9.1 (OUT), R134.2
SI_3: IC10.1 (OUT), R136.2
SI_4: IC11.1 (OUT), R138.2
VCC: C40.+, IM5.IN, IM6.IN, IM7.IN, IM8.IN, JP56.2, JP57.2; also elsewhere on the board

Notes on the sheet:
v1.2
RobotikaBrno RobotikaBrno.cz Robotarna CC BY-SA 4.0
RB3204-RBCX
Released under the Creative Commons Attribution-ShareAlike 4.0 License https://creativecommons.org/licenses/by-sa/4.0/ Designed by: Jaroslav Paral, Jakub Streit RB3204-RBCX https://github.com/RoboticsBrno/RB3204-RBCX
Jaroslav Paral Jakub Streit 9/2020
Fmax = 160 Hz

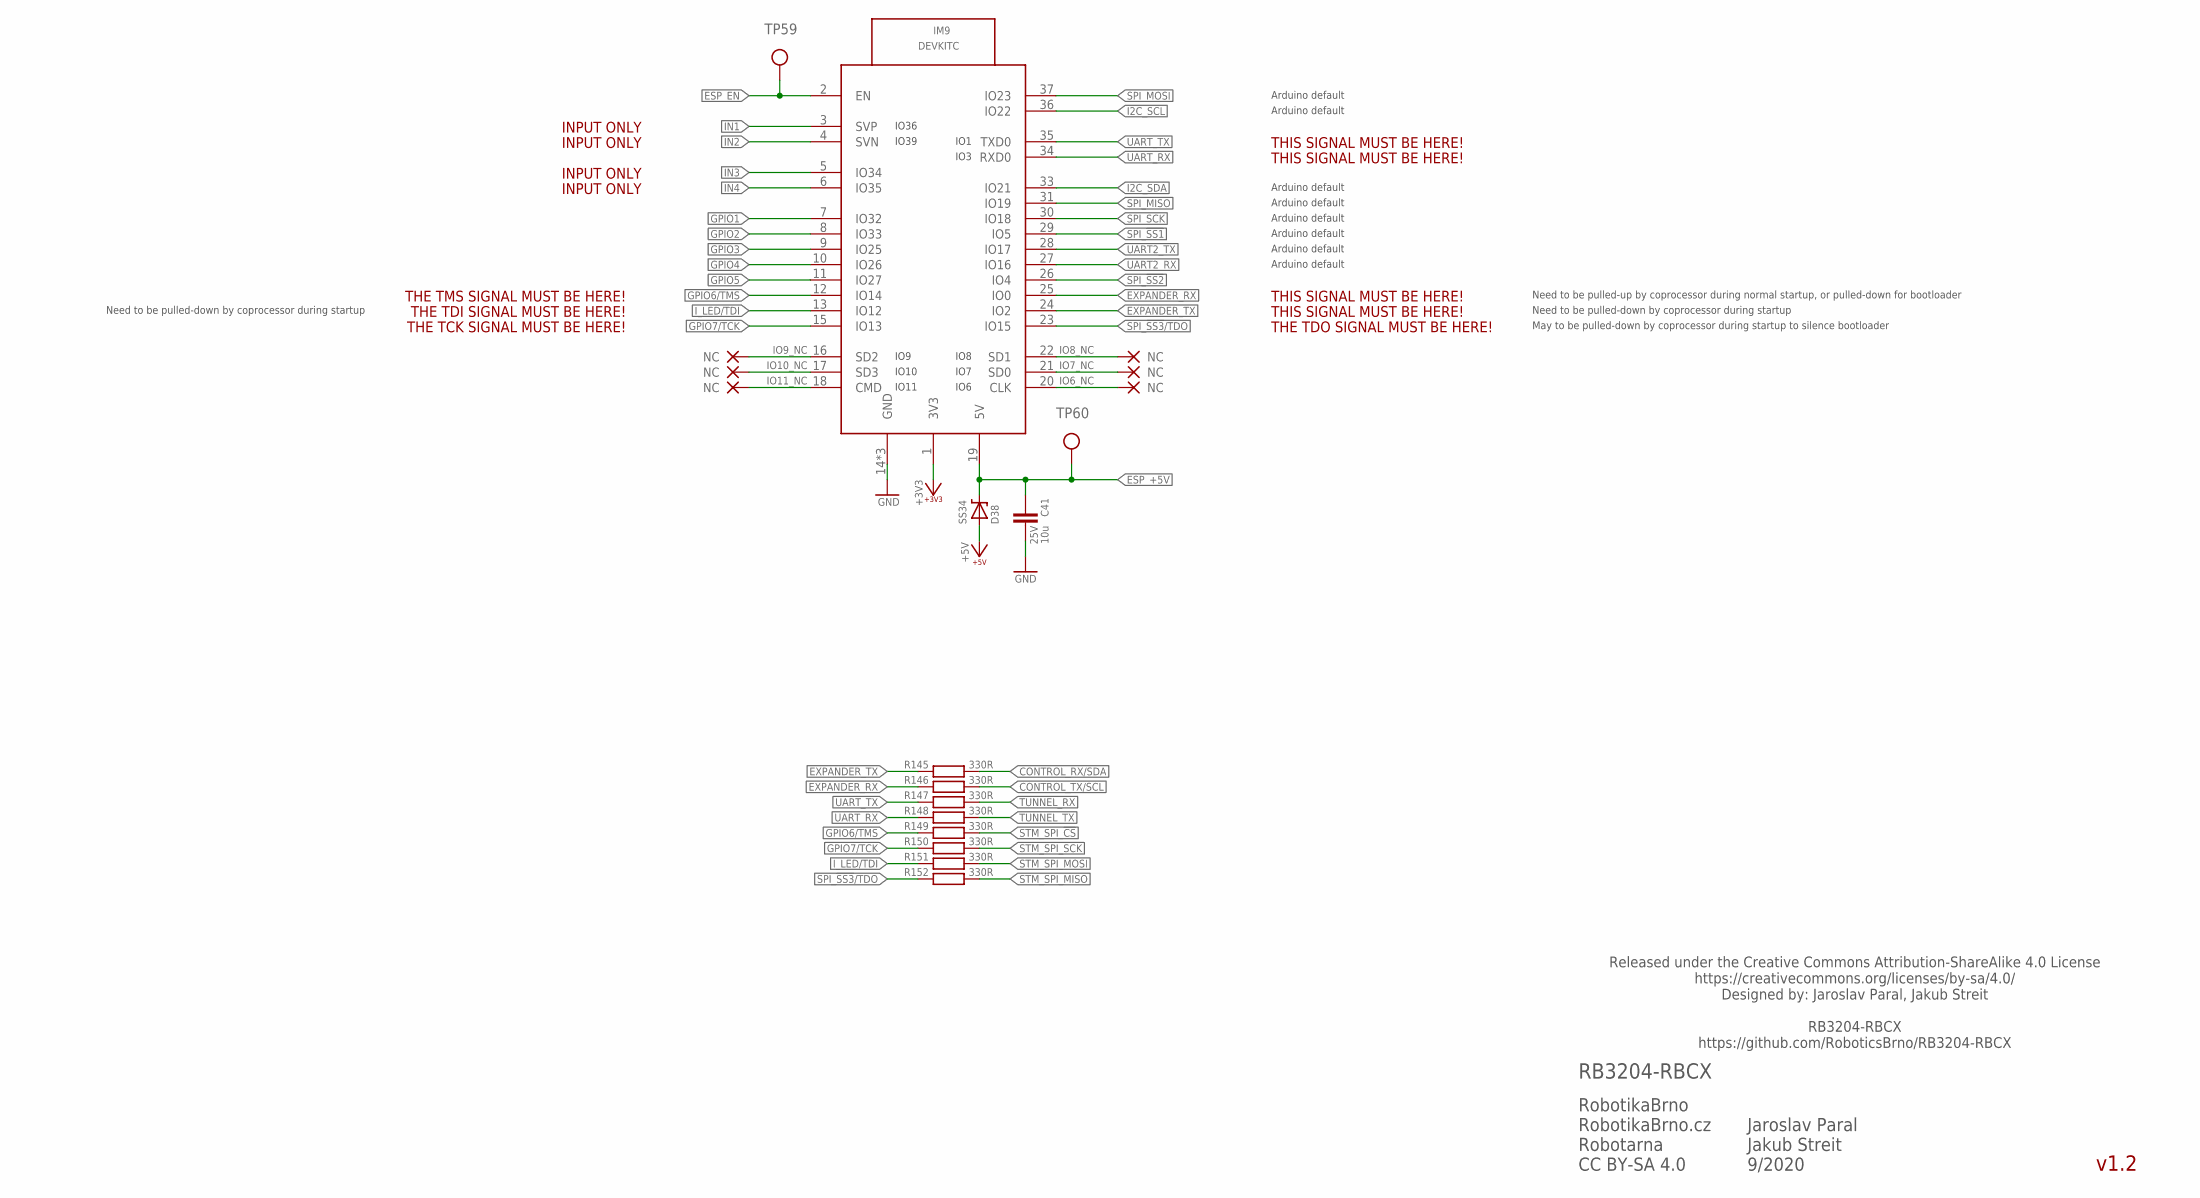
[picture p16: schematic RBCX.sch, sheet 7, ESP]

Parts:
C41: 10u; C0805; VOLTAGE 25V
D38: SS34; SMA
IM9: DEVKITC
R145, R146, R147, R148, R149, R150, R151, R152: 330R; R0402
TP59, TP60: TP_06MM; TP_06

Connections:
+3V3: IM9.1 (3V3); also elsewhere on the board
+5V: D38.A; also elsewhere on the board
CONTROL_RX/SDA: R145.2; also elsewhere on the board
CONTROL_TX/SCL: R146.2; also elsewhere on the board
ESP_+5V: C41.2, D38.C, IM9.19 (5V), TP60.P$1; also elsewhere on the board
ESP_EN: IM9.2 (EN), TP59.P$1; also elsewhere on the board
EXPANDER_RX: IM9.25 (IO0), R146.1
EXPANDER_TX: IM9.24 (IO2), R145.1
GND: C41.1, IM9.14 (GND), IM9.32 (GND), IM9.38 (GND); also elsewhere on the board
GPIO1: IM9.7 (IO32); also elsewhere on the board
GPIO2: IM9.8 (IO33); also elsewhere on the board
GPIO3: IM9.9 (IO25); also elsewhere on the board
GPIO4: IM9.10 (IO26); also elsewhere on the board
GPIO5: IM9.11 (IO27); also elsewhere on the board
GPIO6/TMS: IM9.12 (IO14), R149.1; also elsewhere on the board
GPIO7/TCK: IM9.15 (IO13), R150.1; also elsewhere on the board
I2C_SCL: IM9.36 (IO22); also elsewhere on the board
I2C_SDA: IM9.33 (IO21); also elsewhere on the board
IN1: IM9.3 (SVP); also elsewhere on the board
IN2: IM9.4 (SVN); also elsewhere on the board
IN3: IM9.5 (IO34); also elsewhere on the board
IN4: IM9.6 (IO35); also elsewhere on the board
IO6_NC: IM9.20 (CLK)
IO7_NC: IM9.21 (SD0)
IO8_NC: IM9.22 (SD1)
IO9_NC: IM9.16 (SD2)
IO10_NC: IM9.17 (SD3)
IO11_NC: IM9.18 (CMD)
I_LED/TDI: IM9.13 (IO12), R151.1; also elsewhere on the board
SPI_!SS1: IM9.29 (IO5); also elsewhere on the board
SPI_!SS2: IM9.26 (IO4); also elsewhere on the board
SPI_!SS3!/TDO: IM9.23 (IO15), R152.1; also elsewhere on the board
SPI_MISO: IM9.31 (IO19); also elsewhere on the board
SPI_MOSI: IM9.37 (IO23); also elsewhere on the board
SPI_SCK: IM9.30 (IO18); also elsewhere on the board
STM_SPI_!CS: R149.2; also elsewhere on the board
STM_SPI_MISO: R152.2; also elsewhere on the board
STM_SPI_MOSI: R151.2; also elsewhere on the board
STM_SPI_SCK: R150.2; also elsewhere on the board
TUNNEL_RX: R147.2; also elsewhere on the board
TUNNEL_TX: R148.2; also elsewhere on the board
UART2_RX: IM9.27 (IO16); also elsewhere on the board
UART2_TX: IM9.28 (IO17); also elsewhere on the board
UART_RX: IM9.34 (RXD0), R148.1; also elsewhere on the board
UART_TX: IM9.35 (TXD0), R147.1; also elsewhere on the board

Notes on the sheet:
THE TDI SIGNAL MUST BE HERE!
v1.2
RobotikaBrno RobotikaBrno.cz Robotarna CC BY-SA 4.0
RB3204-RBCX
Released under the Creative Commons Attribution-ShareAlike 4.0 License https://creativecommons.org/licenses/by-sa/4.0/ Designed by: Jaroslav Paral, Jakub Streit RB3204-RBCX https://github.com/RoboticsBrno/RB3204-RBCX
Jaroslav Paral Jakub Streit 9/2020
THIS SIGNAL MUST BE HERE!
INPUT ONLY
Arduino default
THE TCK SIGNAL MUST BE HERE!
THE TDO SIGNAL MUST BE HERE!
THE TMS SIGNAL MUST BE HERE!
Need to be pulled-up by coprocessor during normal startup, or pulled-down for bootloader
Need to be pulled-down by coprocessor during startup
May to be pulled-down by coprocessor during startup to silence bootloader

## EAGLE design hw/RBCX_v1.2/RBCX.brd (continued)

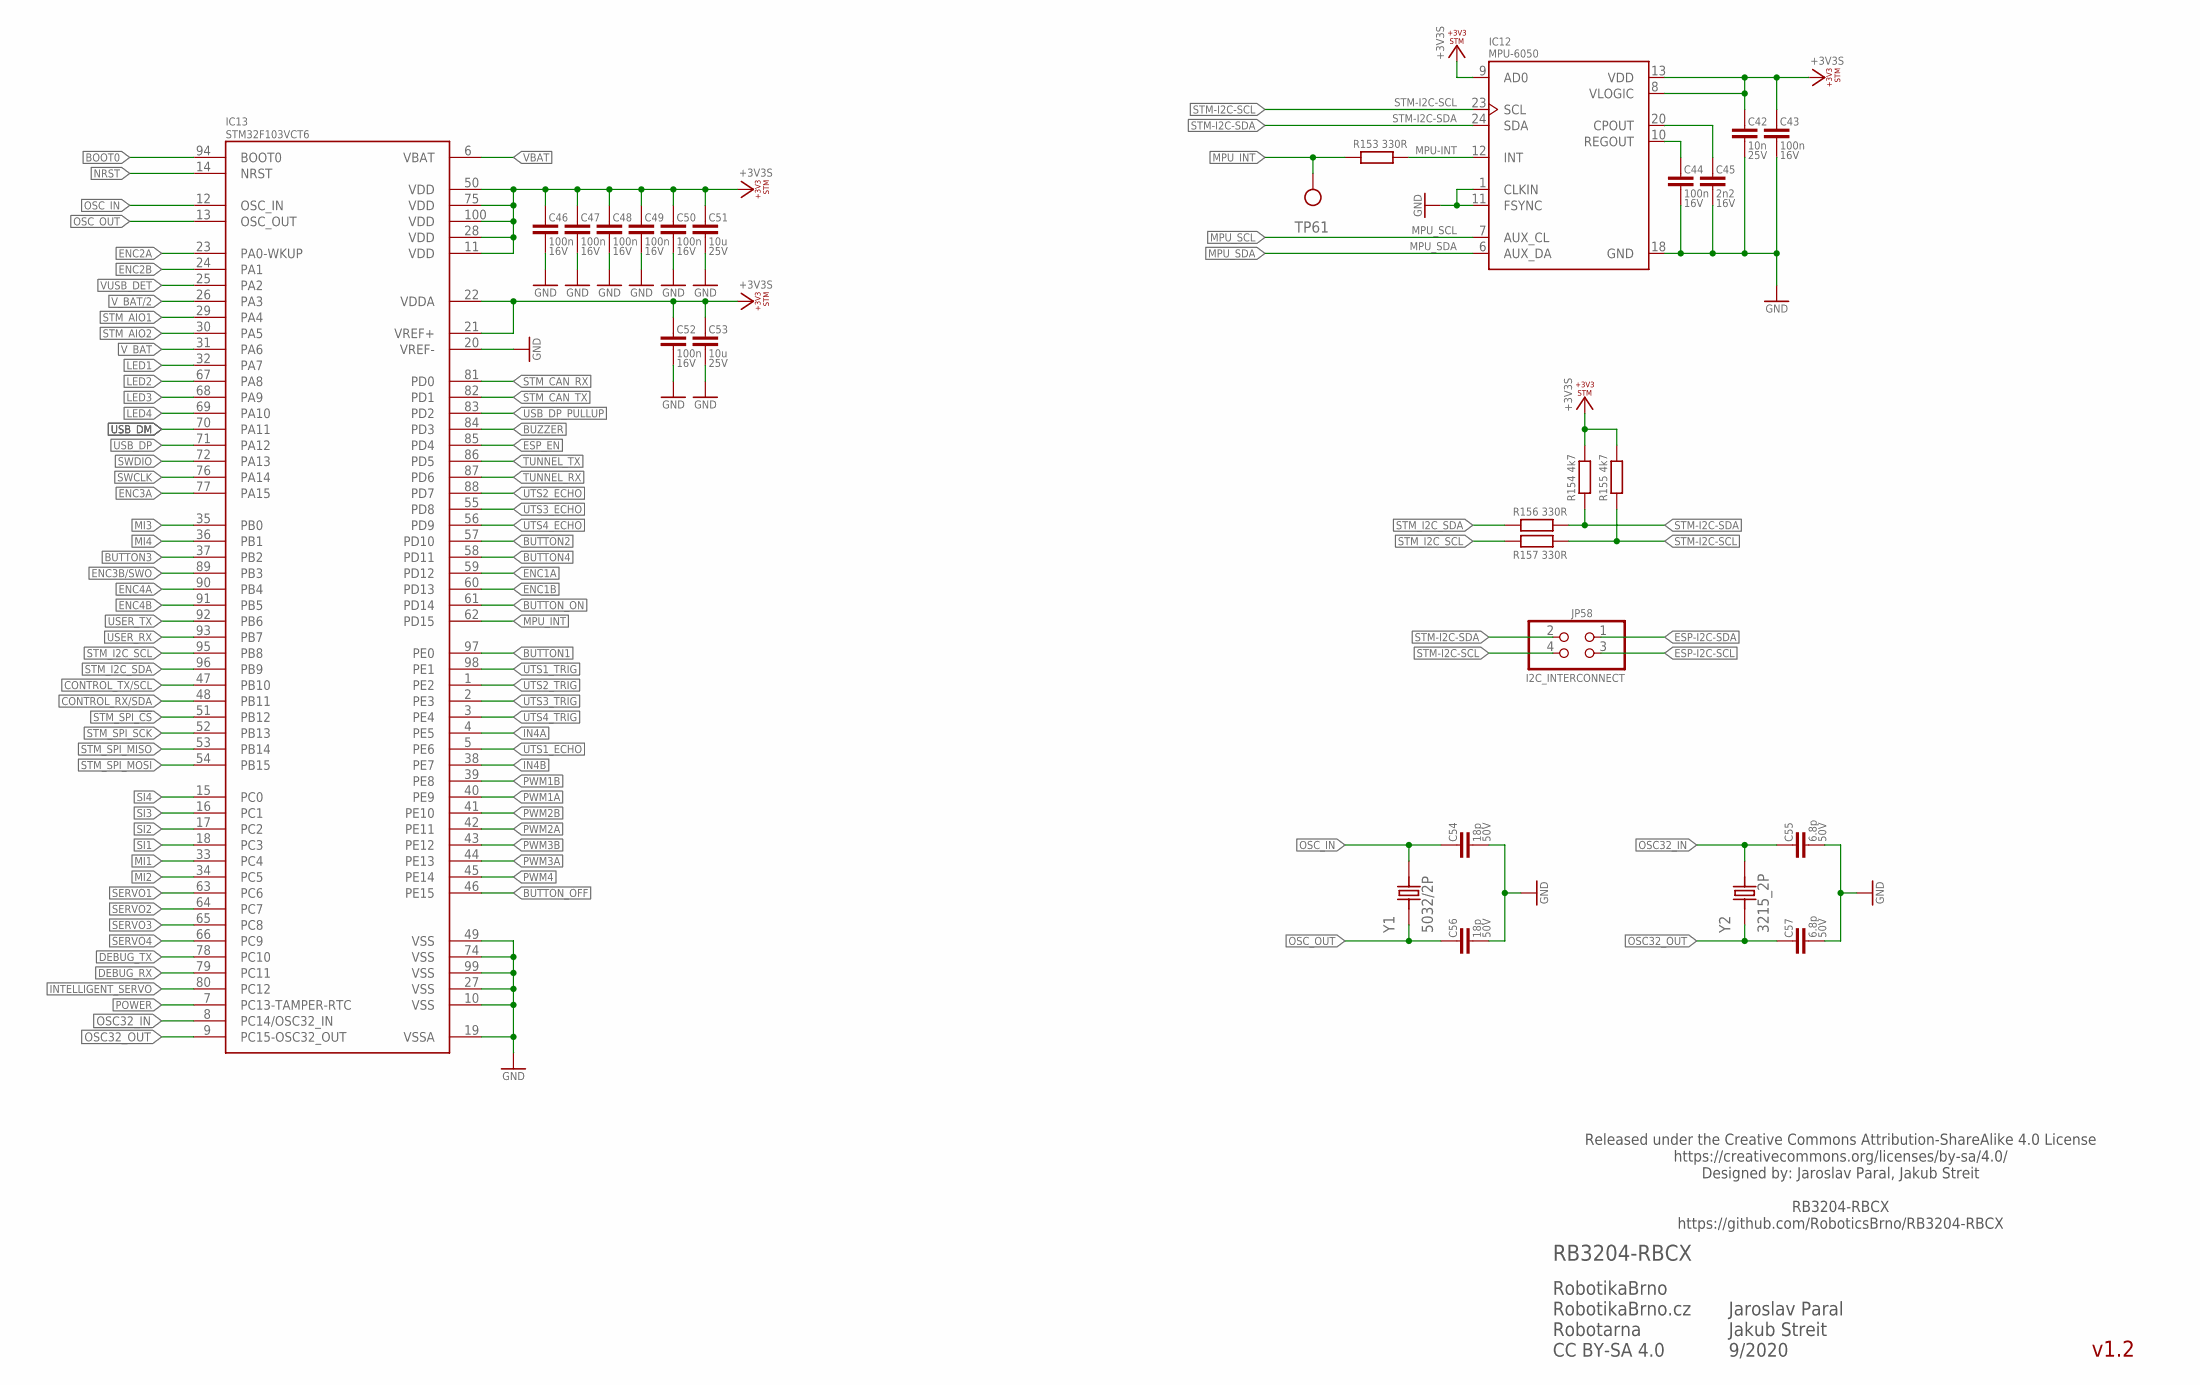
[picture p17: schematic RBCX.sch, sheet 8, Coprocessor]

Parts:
C42: 10n; C0402; VOLTAGE 25V
C43, C44, C46, C47, C48, C49, C50, C52: 100n; C0402; VOLTAGE 16V
C45: 2n2; C0402; VOLTAGE 16V
C51, C53: 10u; C0805; VOLTAGE 25V
C54, C56: 18p; C0402; VOLTAGE 50V
C55, C57: 6.8p; C0402; VOLTAGE 50V
IC12: MPU-6050; QFN50P400X400X95-24N
IC13: STM32F103VCT6; QFP50P1600X1600X160-100N_STM32F103VCT6
JP58: I2C_INTERCONNECT; 2X02
R153, R156, R157: 330R; R0402
R154, R155: 4k7; R0402
TP61: TP_06MM; TP_06
Y1: 5032/2P; OSCCC500X320X135
Y2: 3215_2P; SMD-3215_2P

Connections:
+3V3S: C42.1, C43.2, C46.2, C47.2, C48.2, C49.2, C50.2, C51.2, C52.2, C53.2, IC12.8 (VLOGIC), IC12.9 (AD0), IC12.13 (VDD), IC13.11 (VDD), IC13.21 (VREF+), IC13.22 (VDDA), IC13.28 (VDD), IC13.50 (VDD), IC13.75 (VDD), IC13.100 (VDD), R154.2, R155.2; also elsewhere on the board
BOOT0: IC13.94 (BOOT0); also elsewhere on the board
BUTTON1: IC13.97 (PE0); also elsewhere on the board
BUTTON2: IC13.57 (PD10); also elsewhere on the board
BUTTON3: IC13.37 (PB2); also elsewhere on the board
BUTTON4: IC13.58 (PD11); also elsewhere on the board
BUTTON_OFF: IC13.46 (PE15); also elsewhere on the board
BUTTON_ON: IC13.61 (PD14); also elsewhere on the board
BUZZER: IC13.84 (PD3); also elsewhere on the board
CONTROL_RX/SDA: IC13.48 (PB11); also elsewhere on the board
CONTROL_TX/SCL: IC13.47 (PB10); also elsewhere on the board
CPOUT: C45.2, IC12.20 (CPOUT)
DEBUG_RX: IC13.79 (PC11); also elsewhere on the board
DEBUG_TX: IC13.78 (PC10); also elsewhere on the board
ENC1A: IC13.59 (PD12); also elsewhere on the board
ENC1B: IC13.60 (PD13); also elsewhere on the board
ENC2A: IC13.23 (PA0-WKUP); also elsewhere on the board
ENC2B: IC13.24 (PA1); also elsewhere on the board
ENC3A: IC13.77 (PA15); also elsewhere on the board
ENC3B/SWO: IC13.89 (PB3); also elsewhere on the board
ENC4A: IC13.90 (PB4); also elsewhere on the board
ENC4B: IC13.91 (PB5); also elsewhere on the board
ESP-I2C-SCL: JP58.3; also elsewhere on the board
ESP-I2C-SDA: JP58.1; also elsewhere on the board
ESP_EN: IC13.85 (PD4); also elsewhere on the board
GND: C42.2, C43.1, C44.1, C45.1, C46.1, C47.1, C48.1, C49.1, C50.1, C51.1, C52.1, C53.1, C54.1, C55.1, C56.1, C57.1, IC12.1 (CLKIN), IC12.11 (FSYNC), IC12.18 (GND), IC13.10 (VSS), IC13.19 (VSSA), IC13.20 (VREF-), IC13.27 (VSS), IC13.49 (VSS), IC13.74 (VSS), IC13.99 (VSS); also elsewhere on the board
IN4A: IC13.4 (PE5); also elsewhere on the board
IN4B: IC13.38 (PE7); also elsewhere on the board
INTELLIGENT_SERVO: IC13.80 (PC12); also elsewhere on the board
LED1: IC13.32 (PA7); also elsewhere on the board
LED2: IC13.67 (PA8); also elsewhere on the board
LED3: IC13.68 (PA9); also elsewhere on the board
LED4: IC13.69 (PA10); also elsewhere on the board
MI1: IC13.33 (PC4); also elsewhere on the board
MI2: IC13.34 (PC5); also elsewhere on the board
MI3: IC13.35 (PB0); also elsewhere on the board
MI4: IC13.36 (PB1); also elsewhere on the board
MPU-INT: IC12.12 (INT), R153.2
MPU_INT: IC13.62 (PD15), R153.1, TP61.P$1
MPU_SCL: IC12.7 (AUX_CL); also elsewhere on the board
MPU_SDA: IC12.6 (AUX_DA); also elsewhere on the board
NRST: IC13.14 (NRST); also elsewhere on the board
OSC32_IN: C55.2, IC13.8 (PC14/OSC32_IN), Y2.2
OSC32_OUT: C57.2, IC13.9 (PC15-OSC32_OUT), Y2.1
OSC_IN: C54.2, IC13.12 (OSC_IN), Y1.2
OSC_OUT: C56.2, IC13.13 (OSC_OUT), Y1.1
POWER: IC13.7 (PC13-TAMPER-RTC); also elsewhere on the board
PWM1A: IC13.40 (PE9); also elsewhere on the board
PWM1B: IC13.39 (PE8); also elsewhere on the board
PWM2A: IC13.42 (PE11); also elsewhere on the board
PWM2B: IC13.41 (PE10); also elsewhere on the board
PWM3A: IC13.44 (PE13); also elsewhere on the board
PWM3B: IC13.43 (PE12); also elsewhere on the board
PWM4: IC13.45 (PE14); also elsewhere on the board
REGOUT: C44.2, IC12.10 (REGOUT)
SERVO1: IC13.63 (PC6); also elsewhere on the board
SERVO2: IC13.64 (PC7); also elsewhere on the board
SERVO3: IC13.65 (PC8); also elsewhere on the board
SERVO4: IC13.66 (PC9); also elsewhere on the board
SI1: IC13.18 (PC3); also elsewhere on the board
SI2: IC13.17 (PC2); also elsewhere on the board
SI3: IC13.16 (PC1); also elsewhere on the board
SI4: IC13.15 (PC0); also elsewhere on the board
STM-I2C-SCL: IC12.23 (SCL), JP58.4, R155.1, R157.2; also elsewhere on the board
STM-I2C-SDA: IC12.24 (SDA), JP58.2, R154.1, R156.2; also elsewhere on the board
STM_AIO1: IC13.29 (PA4); also elsewhere on the board
STM_AIO2: IC13.30 (PA5); also elsewhere on the board
STM_CAN_RX: IC13.81 (PD0); also elsewhere on the board
STM_CAN_TX: IC13.82 (PD1); also elsewhere on the board
STM_I2C_SCL: IC13.95 (PB8), R157.1
STM_I2C_SDA: IC13.96 (PB9), R156.1
STM_SPI_!CS: IC13.51 (PB12); also elsewhere on the board
STM_SPI_MISO: IC13.53 (PB14); also elsewhere on the board
STM_SPI_MOSI: IC13.54 (PB15); also elsewhere on the board
STM_SPI_SCK: IC13.52 (PB13); also elsewhere on the board
SWCLK: IC13.76 (PA14); also elsewhere on the board
SWDIO: IC13.72 (PA13); also elsewhere on the board
TUNNEL_RX: IC13.87 (PD6); also elsewhere on the board
TUNNEL_TX: IC13.86 (PD5); also elsewhere on the board
USB_DM: IC13.70 (PA11); also elsewhere on the board
USB_DP: IC13.71 (PA12); also elsewhere on the board
USB_DP_PULLUP: IC13.83 (PD2); also elsewhere on the board
USER_RX: IC13.93 (PB7); also elsewhere on the board
USER_TX: IC13.92 (PB6); also elsewhere on the board
UTS1_ECHO: IC13.5 (PE6); also elsewhere on the board
UTS1_TRIG: IC13.98 (PE1); also elsewhere on the board
UTS2_ECHO: IC13.88 (PD7); also elsewhere on the board
UTS2_TRIG: IC13.1 (PE2); also elsewhere on the board
UTS3_ECHO: IC13.55 (PD8); also elsewhere on the board
UTS3_TRIG: IC13.2 (PE3); also elsewhere on the board
UTS4_ECHO: IC13.56 (PD9); also elsewhere on the board
UTS4_TRIG: IC13.3 (PE4); also elsewhere on the board
VBAT: IC13.6 (VBAT); also elsewhere on the board
VUSB_DET: IC13.25 (PA2); also elsewhere on the board
V_BAT: IC13.31 (PA6); also elsewhere on the board
V_BAT/2: IC13.26 (PA3); also elsewhere on the board

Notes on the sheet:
v1.2
RobotikaBrno RobotikaBrno.cz Robotarna CC BY-SA 4.0
RB3204-RBCX
Released under the Creative Commons Attribution-ShareAlike 4.0 License https://creativecommons.org/licenses/by-sa/4.0/ Designed by: Jaroslav Paral, Jakub Streit RB3204-RBCX https://github.com/RoboticsBrno/RB3204-RBCX
Jaroslav Paral Jakub Streit 9/2020

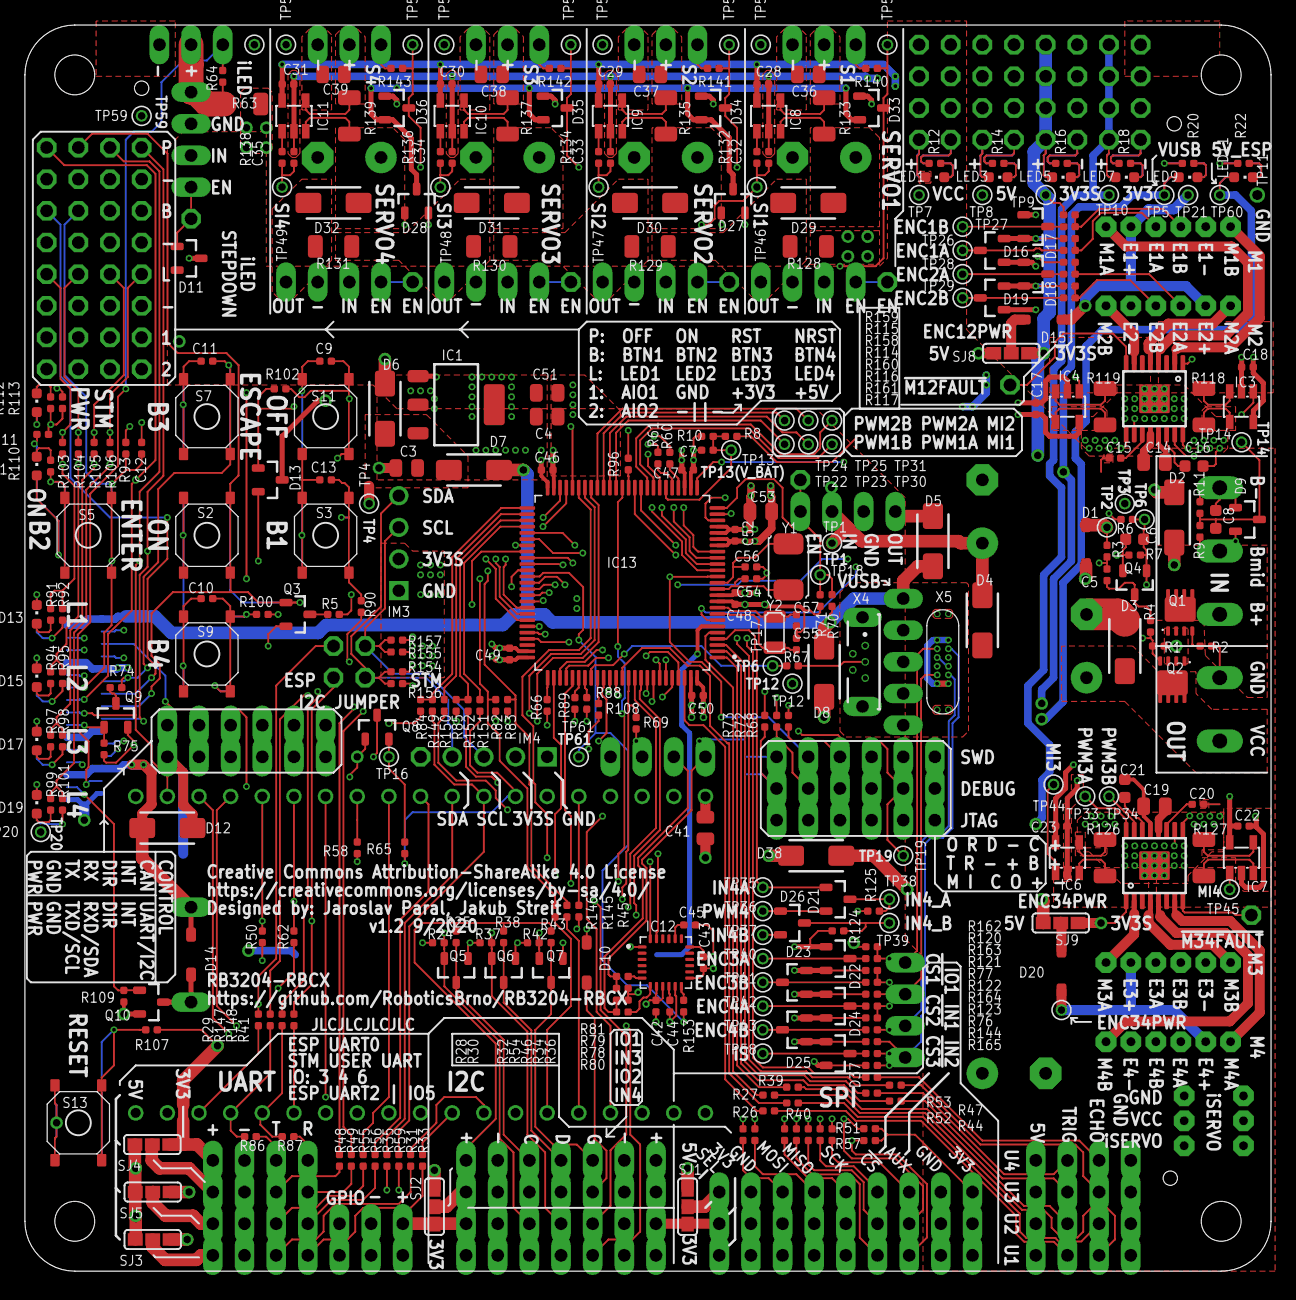
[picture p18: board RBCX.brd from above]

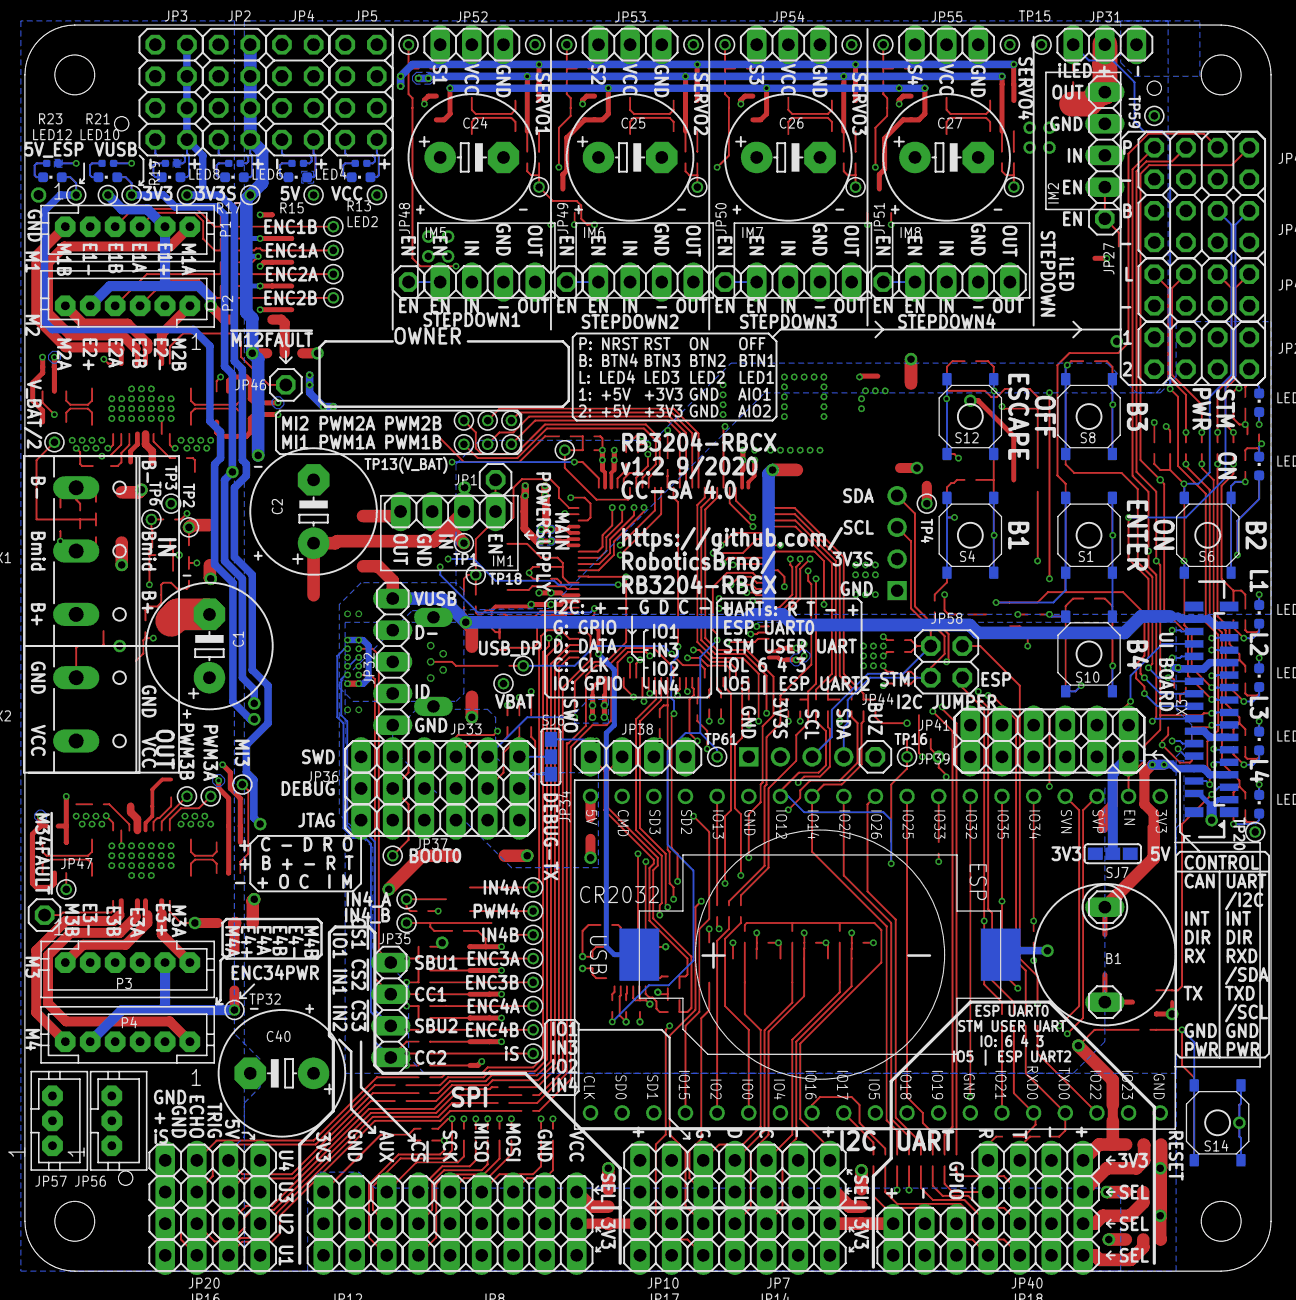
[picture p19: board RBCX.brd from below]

Board: 4 copper layers, 100.0 x 100.0 mm, 471 parts (110 on the bottom side), 294 nets.

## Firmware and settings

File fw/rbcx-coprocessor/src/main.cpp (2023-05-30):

#include <array>

#include "stm32f1xx_hal.h"

#include "utils/Debug.hpp"
#include "utils/TaskWrapper.hpp"

#include "ButtonController.hpp"
#include "I2cController.hpp"
#include "MotorController.hpp"
#include "MpuController.hpp"
#include "OledController.hpp"
#include "StupidServoController.hpp"
#include "UltrasoundController.hpp"

#include "Bsp.hpp"
#include "CdcUartTunnel.hpp"
#include "ControlLink.hpp"
#include "DebugLink.hpp"
#include "Dispatcher.hpp"
#include "Esp32Manager.hpp"
#include "Power.hpp"
#include "SmartServoController.hpp"
#include "UsbCdcLink.h"

static TaskWrapper<3072> mainTask;

int main() {
    clocksInit();
    HAL_Init();

#ifdef RBCX_VECT_TAB_OFFSET
    SCB->VTOR = FLASH_BASE | RBCX_VECT_TAB_OFFSET;
#endif

    pinsInit();

    mainTask.start("main", mainTaskPrio, []() {
        debugUartInit();
        softResetInit();
        powerInit();
        dispatcherInit();
        tunnelUartInit();
        controlUartInit();
        cdcLinkInit();
        I2Cdev_init();
        smartServoInit();
        stupidServoInit();
        ultrasoundInit();
        mpuCreate();
        sEsp32Manager.init();
        motorInit();

        DEBUG("STM32 Coprocessor initialized, v%06x " RBCX_VER_REVISION
                  RBCX_VER_DIRTY_STR "\n",
            RBCX_VER_NUMBER);
        while (true) {
            vTaskDelay(pdMS_TO_TICKS(1));
            debugLinkPoll();
            powerPoll();
            dispatcherPoll();
            tunnelPoll();
            buttonControllerPoll();
            smartServoPoll();
            sEsp32Manager.poll();
        }
    });

    vTaskStartScheduler();
    abort();
}

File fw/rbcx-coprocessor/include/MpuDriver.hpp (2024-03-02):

// I2Cdev library collection - mpu I2C device class
// Based on InvenSense MPU-6050 register map document rev. 2.0, 5/19/2011 (RM-MPU-6000A-00)
// 10/3/2011 by Jeff Rowberg <jeff@rowberg.net>
// 11/28/2014 by Marton Sebok <sebokmarton@gmail.com>
//
// Updates should (hopefully) always be available at https://github.com/jrowberg/i2cdevlib
//
// Changelog:
//     ...        - ongoing debug release
//     2014-11-28 - ported to PIC18 peripheral library from Arduino code
//     2017-03-11 - tested basic functions on STM32

// NOTE: THIS IS ONLY A PARIAL RELEASE. THIS DEVICE CLASS IS CURRENTLY UNDERGOING ACTIVE
// DEVELOPMENT AND IS STILL MISSING SOME IMPORTANT FEATURES. PLEASE KEEP THIS IN MIND IF
// YOU DECIDE TO USE THIS PARTICULAR CODE FOR ANYTHING.

/* ============================================
I2Cdev device library code is placed under the MIT license
Copyright (c) 2012 Jeff Rowberg
Copyright (c) 2014 Marton Sebok

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
THE SOFTWARE IS PROVIDED "AS IS", WITHOUT WARRANTY OF ANY KIND, EXPRESS OR
IMPLIED, INCLUDING BUT NOT LIMITED TO THE WARRANTIES OF MERCHANTABILITY,
FITNESS FOR A PARTICULAR PURPOSE AND NONINFRINGEMENT. IN NO EVENT SHALL THE
AUTHORS OR COPYRIGHT HOLDERS BE LIABLE FOR ANY CLAIM, DAMAGES OR OTHER
LIABILITY, WHETHER IN AN ACTION OF CONTRACT, TORT OR OTHERWISE, ARISING FROM,
OUT OF OR IN CONNECTION WITH THE SOFTWARE OR THE USE OR OTHER DEALINGS IN
THE SOFTWARE.
===============================================
*/

#ifndef _mpu_H_
#define _mpu_H_

#include <stdbool.h>
#include <stdint.h>

#if ((defined mpu_INCLUDE_DMP_MOTIONAPPS20)                                    \
    || (defined mpu_INCLUDE_DMP_MOTIONAPPS41))
#error DMP is not supported yet
#endif

#define mpu_ADDRESS_AD0_LOW                                                    \
    0x68 // address pin low (GND), default for InvenSense evaluation board
#define mpu_ADDRESS_AD0_HIGH 0x69 // address pin high (VCC)
#define mpu_DEFAULT_ADDRESS mpu_ADDRESS_AD0_LOW

#define mpu_RA_XG_OFFS_TC 0x00 //[7] PWR_MODE, [6:1] XG_OFFS_TC, [0] OTP_BNK_VLD
#define mpu_RA_YG_OFFS_TC 0x01 //[7] PWR_MODE, [6:1] YG_OFFS_TC, [0] OTP_BNK_VLD
#define mpu_RA_ZG_OFFS_TC 0x02 //[7] PWR_MODE, [6:1] ZG_OFFS_TC, [0] OTP_BNK_VLD
#define mpu_RA_X_FINE_GAIN 0x03 //[7:0] X_FINE_GAIN
#define mpu_RA_Y_FINE_GAIN 0x04 //[7:0] Y_FINE_GAIN
#define mpu_RA_Z_FINE_GAIN 0x05 //[7:0] Z_FINE_GAIN
#define mpu_RA_XA_OFFS_H 0x06 //[15:0] XA_OFFS
#define mpu_RA_XA_OFFS_L_TC 0x07
#define mpu_RA_YA_OFFS_H 0x08 //[15:0] YA_OFFS
#define mpu_RA_YA_OFFS_L_TC 0x09
#define mpu_RA_ZA_OFFS_H 0x0A //[15:0] ZA_OFFS
#define mpu_RA_ZA_OFFS_L_TC 0x0B
#define mpu_RA_XG_OFFS_USRH 0x13 //[15:0] XG_OFFS_USR
#define mpu_RA_XG_OFFS_USRL 0x14
#define mpu_RA_YG_OFFS_USRH 0x15 //[15:0] YG_OFFS_USR
#define mpu_RA_YG_OFFS_USRL 0x16
#define mpu_RA_ZG_OFFS_USRH 0x17 //[15:0] ZG_OFFS_USR
#define mpu_RA_ZG_OFFS_USRL 0x18
#define mpu_RA_SMPLRT_DIV 0x19
#define mpu_RA_CONFIG 0x1A
#define mpu_RA_GYRO_CONFIG 0x1B
#define mpu_RA_ACCEL_CONFIG 0x1C
#define mpu_RA_FF_THR 0x1D
#define mpu_RA_FF_DUR 0x1E
#define mpu_RA_MOT_THR 0x1F
#define mpu_RA_MOT_DUR 0x20
#define mpu_RA_ZRMOT_THR 0x21
#define mpu_RA_ZRMOT_DUR 0x22
#define mpu_RA_FIFO_EN 0x23
#define mpu_RA_I2C_MST_CTRL 0x24
#define mpu_RA_I2C_SLV0_ADDR 0x25
#define mpu_RA_I2C_SLV0_REG 0x26
#define mpu_RA_I2C_SLV0_CTRL 0x27
#define mpu_RA_I2C_SLV1_ADDR 0x28
#define mpu_RA_I2C_SLV1_REG 0x29
#define mpu_RA_I2C_SLV1_CTRL 0x2A
#define mpu_RA_I2C_SLV2_ADDR 0x2B
#define mpu_RA_I2C_SLV2_REG 0x2C
#define mpu_RA_I2C_SLV2_CTRL 0x2D
#define mpu_RA_I2C_SLV3_ADDR 0x2E
#define mpu_RA_I2C_SLV3_REG 0x2F
#define mpu_RA_I2C_SLV3_CTRL 0x30
#define mpu_RA_I2C_SLV4_ADDR 0x31
#define mpu_RA_I2C_SLV4_REG 0x32
#define mpu_RA_I2C_SLV4_DO 0x33
#define mpu_RA_I2C_SLV4_CTRL 0x34
#define mpu_RA_I2C_SLV4_DI 0x35
#define mpu_RA_I2C_MST_STATUS 0x36
#define mpu_RA_INT_PIN_CFG 0x37
#define mpu_RA_INT_ENABLE 0x38
#define mpu_RA_DMP_INT_STATUS 0x39
#define mpu_RA_INT_STATUS 0x3A
#define mpu_RA_ACCEL_XOUT_H 0x3B
#define mpu_RA_ACCEL_XOUT_L 0x3C
#define mpu_RA_ACCEL_YOUT_H 0x3D
#define mpu_RA_ACCEL_YOUT_L 0x3E
#define mpu_RA_ACCEL_ZOUT_H 0x3F
#define mpu_RA_ACCEL_ZOUT_L 0x40
#define mpu_RA_TEMP_OUT_H 0x41
#define mpu_RA_TEMP_OUT_L 0x42
#define mpu_RA_GYRO_XOUT_H 0x43
#define mpu_RA_GYRO_XOUT_L 0x44
#define mpu_RA_GYRO_YOUT_H 0x45
#define mpu_RA_GYRO_YOUT_L 0x46
#define mpu_RA_GYRO_ZOUT_H 0x47
#define mpu_RA_GYRO_ZOUT_L 0x48
#define mpu_RA_EXT_SENS_DATA_00 0x49
#define mpu_RA_EXT_SENS_DATA_01 0x4A
#define mpu_RA_EXT_SENS_DATA_02 0x4B
#define mpu_RA_EXT_SENS_DATA_03 0x4C
#define mpu_RA_EXT_SENS_DATA_04 0x4D
#define mpu_RA_EXT_SENS_DATA_05 0x4E
#define mpu_RA_EXT_SENS_DATA_06 0x4F
#define mpu_RA_EXT_SENS_DATA_07 0x50
#define mpu_RA_EXT_SENS_DATA_08 0x51
#define mpu_RA_EXT_SENS_DATA_09 0x52
#define mpu_RA_EXT_SENS_DATA_10 0x53
#define mpu_RA_EXT_SENS_DATA_11 0x54
#define mpu_RA_EXT_SENS_DATA_12 0x55
#define mpu_RA_EXT_SENS_DATA_13 0x56
#define mpu_RA_EXT_SENS_DATA_14 0x57
#define mpu_RA_EXT_SENS_DATA_15 0x58
#define mpu_RA_EXT_SENS_DATA_16 0x59
#define mpu_RA_EXT_SENS_DATA_17 0x5A
#define mpu_RA_EXT_SENS_DATA_18 0x5B
#define mpu_RA_EXT_SENS_DATA_19 0x5C
#define mpu_RA_EXT_SENS_DATA_20 0x5D
#define mpu_RA_EXT_SENS_DATA_21 0x5E
#define mpu_RA_EXT_SENS_DATA_22 0x5F
#define mpu_RA_EXT_SENS_DATA_23 0x60
#define mpu_RA_MOT_DETECT_STATUS 0x61
#define mpu_RA_I2C_SLV0_DO 0x63
#define mpu_RA_I2C_SLV1_DO 0x64
#define mpu_RA_I2C_SLV2_DO 0x65
#define mpu_RA_I2C_SLV3_DO 0x66
#define mpu_RA_I2C_MST_DELAY_CTRL 0x67
#define mpu_RA_SIGNAL_PATH_RESET 0x68
#define mpu_RA_MOT_DETECT_CTRL 0x69
#define mpu_RA_USER_CTRL 0x6A
#define mpu_RA_PWR_MGMT_1 0x6B
#define mpu_RA_PWR_MGMT_2 0x6C
#define mpu_RA_BANK_SEL 0x6D
#define mpu_RA_MEM_START_ADDR 0x6E
#define mpu_RA_MEM_R_W 0x6F
#define mpu_RA_DMP_CFG_1 0x70
#define mpu_RA_DMP_CFG_2 0x71
#define mpu_RA_FIFO_COUNTH 0x72
#define mpu_RA_FIFO_COUNTL 0x73
#define mpu_RA_FIFO_R_W 0x74
#define mpu_RA_WHO_AM_I 0x75

#define mpu_TC_PWR_MODE_BIT 7
#define mpu_TC_OFFSET_BIT 6
#define mpu_TC_OFFSET_LENGTH 6
#define mpu_TC_OTP_BNK_VLD_BIT 0

#define mpu_VDDIO_LEVEL_VLOGIC 0
#define mpu_VDDIO_LEVEL_VDD 1

#define mpu_CFG_EXT_SYNC_SET_BIT 5
#define mpu_CFG_EXT_SYNC_SET_LENGTH 3
#define mpu_CFG_DLPF_CFG_BIT 2
#define mpu_CFG_DLPF_CFG_LENGTH 3

#define mpu_EXT_SYNC_DISABLED 0x0
#define mpu_EXT_SYNC_TEMP_OUT_L 0x1
#define mpu_EXT_SYNC_GYRO_XOUT_L 0x2
#define mpu_EXT_SYNC_GYRO_YOUT_L 0x3
#define mpu_EXT_SYNC_GYRO_ZOUT_L 0x4
#define mpu_EXT_SYNC_ACCEL_XOUT_L 0x5
#define mpu_EXT_SYNC_ACCEL_YOUT_L 0x6
#define mpu_EXT_SYNC_ACCEL_ZOUT_L 0x7

#define mpu_DLPF_BW_256 0x00
#define mpu_DLPF_BW_188 0x01
#define mpu_DLPF_BW_98 0x02
#define mpu_DLPF_BW_42 0x03
#define mpu_DLPF_BW_20 0x04
#define mpu_DLPF_BW_10 0x05
#define mpu_DLPF_BW_5 0x06

#define mpu_GCONFIG_FS_SEL_BIT 4
#define mpu_GCONFIG_FS_SEL_LENGTH 2

#define mpu_GYRO_FS_250 0x00
#define mpu_GYRO_FS_500 0x01
#define mpu_GYRO_FS_1000 0x02
#define mpu_GYRO_FS_2000 0x03
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

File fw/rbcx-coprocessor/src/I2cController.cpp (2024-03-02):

// I2Cdev library collection - Main I2C device class header file
// Abstracts bit and byte I2C R/W functions into a convenient class
// 6/9/2012 by Jeff Rowberg <jeff@rowberg.net>
// 6/6/2015 by Andrey Voloshin <voloshin@think.in.ua>
//
// Changelog:
//      2015-06-06 - ported to STM32 HAL library from Arduino code

/* ============================================
I2Cdev device library code is placed under the MIT license
Copyright (c) 2013 Jeff Rowberg

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
THE SOFTWARE IS PROVIDED "AS IS", WITHOUT WARRANTY OF ANY KIND, EXPRESS OR
IMPLIED, INCLUDING BUT NOT LIMITED TO THE WARRANTIES OF MERCHANTABILITY,
FITNESS FOR A PARTICULAR PURPOSE AND NONINFRINGEMENT. IN NO EVENT SHALL THE
AUTHORS OR COPYRIGHT HOLDERS BE LIABLE FOR ANY CLAIM, DAMAGES OR OTHER
LIABILITY, WHETHER IN AN ACTION OF CONTRACT, TORT OR OTHERWISE, ARISING FROM,
OUT OF OR IN CONNECTION WITH THE SOFTWARE OR THE USE OR OTHER DEALINGS IN
THE SOFTWARE.
===============================================
*/
#include "I2cController.hpp"
#include "Bsp.hpp"
#include "MpuController.hpp"
#include "OledController.hpp"
#include "utils/Debug.hpp"

#include "timers.h"
#include "utils/MutexWrapper.hpp"
#include "utils/QueueWrapper.hpp"
#include "utils/SemaphoreWrapper.hpp"
#include "utils/TaskWrapper.hpp"

// #include "event_groups.h"
#include <mutex>

static TaskWrapper<1024> i2cTask;

static QueueWrapper<CoprocReq_I2cReq, 16> i2cQueue;
static MutexWrapper i2cMutex;
static BinarySemaphoreWrapper i2cTxSemaphore;

// Hold pointer to inited HAL I2C device
I2C_HandleTypeDef I2Cdev_hi2c;

void i2cSetEventFlag(I2cEvents flag) {
    xTaskNotify(i2cTask.handle(), flag, eSetBits);
}

void i2cSetEventFlagFromIsr(I2cEvents flag) {
    BaseType_t woken = 0;
    xTaskNotifyFromISR(i2cTask.handle(), flag, eSetBits, &woken);
    portYIELD_FROM_ISR(woken);
}

void i2cDispatch(const CoprocReq_I2cReq& req) {
    if (i2cQueue.push_back(req, 0)) {
        i2cSetEventFlag(I2C_MESSAGE);
    } else {
        DEBUG("I2c queue overflow\n");
    }
}

/** Default timeout value for read operations.
 * Set this to 0 to disable timeout detection.
 */
uint16_t I2Cdev_readTimeout = I2CDEV_DEFAULT_READ_TIMEOUT;

uint8_t I2Cdev_init() {
    I2Cdev_hi2c.Instance = I2C1;
    I2Cdev_hi2c.Init.ClockSpeed = 400000;
    I2Cdev_hi2c.Init.DutyCycle = I2C_DUTYCYCLE_2;
    I2Cdev_hi2c.Init.OwnAddress1 = 0;
    I2Cdev_hi2c.Init.AddressingMode = I2C_ADDRESSINGMODE_7BIT;
    I2Cdev_hi2c.Init.DualAddressMode = I2C_DUALADDRESS_DISABLE;
    I2Cdev_hi2c.Init.OwnAddress2 = 0;
    I2Cdev_hi2c.Init.GeneralCallMode = I2C_GENERALCALL_DISABLE;
    I2Cdev_hi2c.Init.NoStretchMode = I2C_NOSTRETCH_DISABLE;
    auto init = HAL_I2C_Init(&I2Cdev_hi2c);

    if (init == HAL_OK) {
        i2cQueue.create();
        i2cMutex.create();
        i2cTxSemaphore.create();

        i2cTask.start("i2c", i2cPrio, []() {
            CoprocReq_I2cReq req;
            EventBits_t eventsBit = I2C_NONE;

            while (true) {
                if (xTaskNotifyWait(0, 0xFFFFFFFF, &eventsBit, portMAX_DELAY)
                    == pdFAIL) {
                    continue;
                }

                if (eventsBit & I2C_MPU_TICK) {
                    mpuTick();
                }

                if (eventsBit & I2C_MESSAGE) {
                    while (i2cQueue.pop_front(req, 0)) {
                        switch (req.which_payload) {
                        case CoprocReq_I2cReq_oledReq_tag:
                            oledDispatch(req.payload.oledReq);
                            break;
                        case CoprocReq_I2cReq_mpuReq_tag:
                            mpuDispatch(req.payload.mpuReq);
                            // DEBUGLN("MPU Req %d", req.payload.mpuReq.which_mpuCmd);
                            break;
                        }
                    }
                }
                // vTaskDelay(pdMS_TO_TICKS(10));
            }
        });
    } else {
        DEBUG("Error I2c Init\n");
    }
}

extern "C" void I2C1_EV_IRQHandler() { HAL_I2C_EV_IRQHandler(&I2Cdev_hi2c); }
extern "C" void I2C1_ER_IRQHandler() { HAL_I2C_ER_IRQHandler(&I2Cdev_hi2c); }

extern "C" __weak void HAL_I2C_MasterTxCpltCallback(I2C_HandleTypeDef* hi2c) {
    i2cTxSemaphore.giveFromIsr();
}

extern "C" __weak void HAL_I2C_MasterRxCpltCallback(I2C_HandleTypeDef* hi2c) {
    i2cTxSemaphore.giveFromIsr();
}

extern "C" __weak void HAL_I2C_MemTxCpltCallback(I2C_HandleTypeDef* hi2c) {
    i2cTxSemaphore.giveFromIsr();
}

extern "C" __weak void HAL_I2C_MemRxCpltCallback(I2C_HandleTypeDef* hi2c) {
    i2cTxSemaphore.giveFromIsr();
}

extern "C" __weak void HAL_I2C_ErrorCallback(I2C_HandleTypeDef* hi2c) {
    i2cTxSemaphore.giveFromIsr();
}

template <typename F> uint8_t i2cWrap(F fun, uint32_t Timeout) {
    std::scoped_lock lock(i2cMutex);

    uint16_t tout = Timeout > 0 ? Timeout : I2CDEV_DEFAULT_READ_TIMEOUT;

    auto beginStatus = fun();
    if (beginStatus == HAL_OK) {
        auto ok = i2cTxSemaphore.take(pdMS_TO_TICKS(tout));

        if (!ok) {
            DEBUG("I2C timeout\n");
            HAL_I2C_Master_Abort_IT(&I2Cdev_hi2c, 0);
        }
        return ok;
    } else {
        HAL_I2C_Master_Abort_IT(&I2Cdev_hi2c, 0);
        return 0;
    }
}

void i2cReset() { i2cQueue.reset(); }

/* Rewrited original functions */
uint8_t I2Cdev_Master_Transmit(
    uint16_t DevAddress, uint8_t* pData, uint16_t Size, uint32_t Timeout) {
    return i2cWrap(
        [=]() {
            auto beginStatus = HAL_I2C_Master_Transmit_IT(
                &I2Cdev_hi2c, DevAddress << 1, pData, Size);

            if (beginStatus != HAL_OK) {
                DEBUG("I2C ERR - Tx %d bytes, ret: %d %d %d\n", Size,
                    beginStatus, HAL_I2C_GetError(&I2Cdev_hi2c),
                    HAL_I2C_GetState(&I2Cdev_hi2c));
            }
            return beginStatus;
        },
        Timeout);
}

uint8_t I2Cdev_Master_Receive(
    uint16_t DevAddress, uint8_t* pData, uint16_t Size, uint32_t Timeout) {
    return i2cWrap(
        [=]() {
            auto beginStatus = HAL_I2C_Master_Receive_IT(
                &I2Cdev_hi2c, DevAddress << 1, pData, Size);

            if (beginStatus != HAL_OK) {
                DEBUG("I2C ERR - Rx %d bytes, ret: %d %d %d\n", Size,
                    beginStatus, HAL_I2C_GetError(&I2Cdev_hi2c),
                    HAL_I2C_GetState(&I2Cdev_hi2c));
            }
            return beginStatus;
        },
        Timeout);
}

uint8_t I2Cdev_Mem_Write(uint16_t DevAddress, uint16_t MemAddress,
    uint16_t MemAddSize, uint8_t* pData, uint16_t Size, uint32_t Timeout) {
    return i2cWrap(
        [=]() {
            auto beginStatus = HAL_I2C_Mem_Write_IT(&I2Cdev_hi2c,
                DevAddress << 1, MemAddress, MemAddSize, pData, Size);

            if (beginStatus != HAL_OK) {
                DEBUG("I2C ERR - Mem write %d bytes, ret: %d\n", Size,
                    beginStatus);
            }
            return beginStatus;
        },
        Timeout);
}
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

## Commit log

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2020-03-06 MainBoardSCH: Add first part of schema with STM32F103VCT6
    [MainBoard.brd, MainBoard.sch]
2020-03-06 MainBoardSCH: Add all required peripheries to STM MCU, finish encoder pinouts
    TODO:
    - fix motor PWMs output for DRV8833
    - add ESP32 connectors
    - add ultrasonic connectors
    - add servo connectors
    [MainBoard.brd, MainBoard.sch]
2020-03-06 MainBoard: Rename files from `MainBoard` to `RBCX-MainBoard`
    - better distinguishing from RBControl files
    [RBCX-MainBoard.brd, RBCX-MainBoard.sch]
2020-03-06 MainBoardSCH: Add connectors for US and Servo + step downs
    [RBCX-MainBoard.brd, RBCX-MainBoard.sch]
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2020-03-08 MainBoard: Fix INA180 package
    [RBCX-MainBoard.brd, RBCX-MainBoard.sch]
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2020-03-09 MainBoardSCH: Fix PWMs and encoders signals overvoltage protection power
    [RBCX-MainBoard.brd, RBCX-MainBoard.sch]
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2020-03-13 MainBoardSCH: Add ability to redirect DEBUG_TX to SWO signal at SWD connector
    [RBCX-MainBoard.brd, RBCX-MainBoard.sch]
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2020-03-17 MainBoardSCH: Add diode in SOD-123 (B5819W) and replace some +5V0S with +5V
    [RBCX-MainBoard.brd, RBCX-MainBoard.sch]
2020-03-17 MainBoardSCH: Replace diode in SOD-123 with standard part from eagle_libraries
    [RBCX-MainBoard.brd, RBCX-MainBoard.sch]
2020-03-17 MainBoardSCH: Replace +5V0S power rail with +5V
    [RBCX-MainBoard.brd, RBCX-MainBoard.sch]
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2020-03-17 MainBoardSCH: Add main voltage regulators and power LEDs
    [RBCX-MainBoard.brd, RBCX-MainBoard.sch]
2020-03-17 MainBoardSCH: Add bulk capacitor to stepdowns and drivers
    [RBCX-MainBoard.brd, RBCX-MainBoard.sch]
2020-03-17 MainBoardSCH: Add buzzer
    [RBCX-MainBoard.brd, RBCX-MainBoard.sch]
2020-03-17 MainBoardSCH: Add ESP UART and expander uart connector
    [RBCX-MainBoard.brd, RBCX-MainBoard.sch]
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2020-03-18 MainBoardSCH: Renumber parts MainBoardBRD: Move all parts to one group next to the board
    [RBCX-MainBoard.brd, RBCX-MainBoard.sch]
2020-03-18 MainBoardBRD: Place most of the parts to the board
    [RBCX-MainBoard.brd, RBCX-MainBoard.sch]
2020-03-21 FW: DRV8833-PWM-test fw - fix generating PWM :]
2020-03-23 MainBoardBRD: Fix invalid attributes position
    [RBCX-MainBoard.brd]
2020-03-23 MainBoard: Remove iLed stepdown and some bulk capacitors, change bulk capacitors package to THT
    [RBCX-MainBoard.brd, RBCX-MainBoard.sch]
2020-03-23 MainBoard: Replace UIboard connector and expander connector with FFC/FPC connectors
    [RBCX-MainBoard.brd, RBCX-MainBoard.sch]
2020-03-23 MainBoard: Replace SMD buttons with THT
    [RBCX-MainBoard.brd, RBCX-MainBoard.sch]
2020-03-23 MainBoardBRD: Mirror THT connectors and capacitors, battery holder and buzzer
    [RBCX-MainBoard.brd]
2020-03-23 MainBoardBRD: move mounting holes closer to the board edge
    [RBCX-MainBoard.brd]
2020-03-23 MainBoard: Remove motors terminal block, leave only pinheads
    [RBCX-MainBoard.brd, RBCX-MainBoard.sch]
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2020-03-24 MainBoardSCH: Add P channel power MOSFETs gate voltage spikes protection
    [RBCX-MainBoard.brd, RBCX-MainBoard.sch]
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2020-03-24 MainBoardSCH: Add missing P channel MOSFETs attributes (PADS, EXTENDED, MF)
    [RBCX-MainBoard.brd, RBCX-MainBoard.sch]
2020-03-25 MainBoard: Change resistors package to 0402, because of space and price
    [RBCX-MainBoard.brd, RBCX-MainBoard.sch]
2020-03-27 MainBoard: Add BOM, update parts value and package
    [RBCX-MainBoard.brd, RBCX-MainBoard.sch, parts.xlsx]
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2020-03-29 MainBoard: Improve BOM
    - check whole `parts.xlsx` file with JLCPCB web and `RBCX-MainBoard.sch`
    [parts.xlsx]
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2020-04-08 MainBoardBRD: change top side SMD parts footprint according IPC-7351 (using Library Expert Pro (2019.7) )
    [RBCX-MainBoard.brd, RBCX-MainBoard.sch]
2020-04-12 MainBoardBRD: route power supply parts
    Routed:
    - on/off power transistor Q1. Q2
    - power supply step-ups
    - servos power supply
    - apply `robotikabrno.dru`
    [RBCX-MainBoard.brd]
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2020-04-15 MainBoard: 4 layers, motors connector, DRV8833, libraries
    - set 4 layers stack + change DRC setting about same signals, the rest is still same (possible place
    for improvements due to 4 layers stack and https://jlcpcb.com/capabilities/Capabilities)
    - motors connectors - remove terminal blocks, replace pinheads with JST-PH6 (2mm x 6 pins)
    - DRV8833
    - improve `DRV8833.lbr` library - fix thermal GND pad under the package
    - reroute on DPS and add thermal VIAs according http://www.ti.com/lit/an/slma004b/slma004b.pdf
    - reroute `Q1` and `Q2` + main power terminal block
    - libraries - add `jst-ph.lbr` and document `LIBRARIES.md` with source info about used libraries
    - please extend the `LIBRARIE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
    [RBCX-MainBoard.brd, RBCX-MainBoard.sch]
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2020-04-18 MainBoardBRD: update DRC and reroute DRV8833 driver power supply
    - update DRC and save it as `robotikabrno-4-layers.dru`
    - optimize values according manufactors 4 layers stack capabilities
    [RBCX-MainBoard.brd]
2020-04-18 MainBoard: Change power circuit to make ON button connected to GND
    [RBCX-MainBoard.brd, RBCX-MainBoard.sch]
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2020-04-18 MainBoardBRD: routing power - VCC, 5V, servo, DRV8833
    [RBCX-MainBoard.brd, RBCX-MainBoard.sch]
2020-04-19 MainBoardBRD: routing power - +5V, +3V3_ESP, +3V3_STM, DRV8833
    - change DRC - `robotikabrno-4-layers.dru`
    [RBCX-MainBoard.brd]
2020-04-22 MainBoard: - change pinout of ESP and STM - change pinout of UIboard connector - add support for ESP debugging over JTAG through STM - add USB cable insertion detection - add 1k5 pull resistor to USB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
    [RBCX-MainBoard.brd, RBCX-MainBoard.sch, parts.xlsx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]
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2020-04-30 MainBoardSCH: Change UTS, BUTTONS and IMU_INT pins, swap BUTTON-ON and BUTTON-OFF at JP21, swap SCL and SDA at X3, swap GPIO-1 and GPIO-7 between JP28 and JP30 MainBoardBRD: routing (buses, buttons a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
    [RBCX-MainBoard.brd, RBCX-MainBoard.sch, pinout.xlsx]
2020-04-30 MainBoard: Add leds and uUSB to bottom side, move the leftmost pinheads far from the board edge, fix DRC error in DRV8833 library, swap position of servos and motors + power connectors
    [RBCX-MainBoard.brd, RBCX-MainBoard.sch]
2020-05-01 MainBoard: Add servo as a design block, renumber schematic
    [RBCX-MainBoard.brd, RBCX-MainBoard.sch]
2020-05-02 MainBoard: Add power LEDs for VUSB and +5V_ESP and secondary power LEDS for +3v3S and VCC
    [RBCX-MainBoard.brd, RBCX-MainBoard.sch]
2020-05-03 Fix function name convention
    Fix function name convention
    Fix method naming convention
    Fix pinInit()
    Fix cdcLinkPoll name
    [main.cpp]
2020-05-03 Fix file naming convention
    Fix file naming convention
    Fix file naming convention
    Fix include capitalization in main
    Fix file naming
    Delete incorrectly name file
    [Bsp.hpp, UsbCdcLink.c, main.cpp]
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2020-05-06 MainBoard: Swap IN4A and IN4B, routed motors + servos
    [RBCX-MainBoard.brd, RBCX-MainBoard.sch, pinout.xlsx]
2020-05-06 MainBoardBRD: Rotate servos step-down to shorten power trace
    [RBCX-MainBoard.brd, RBCX-MainBoard.sch]
2020-05-06 MainBoard: Fix USB connectors packages, add Design block backup file extensions to gitignore
    [RBCX-MainBoard.brd, RBCX-MainBoard.sch]
2020-05-06 MainBoard: Compete USB, swap VUSB_DET and BUTTON_ON, all parts on board
    [RBCX-MainBoard.brd, RBCX-MainBoard.sch, pinout.xlsx]
2020-05-06 MainBoard: Mirror motor connectors (to the bottom side) and swap signals to keep previous routing
    [RBCX-MainBoard.brd, RBCX-MainBoard.sch]
2020-05-06 MainBoard: Mirror iLed step-down (to the bottom side)
    [RBCX-MainBoard.brd]
2020-05-06 MainBoard: Routing (coprocessor power), remove one output capacitor from LDO - shared with STM
    [RBCX-MainBoard.brd, RBCX-MainBoard.sch]
2020-05-07 MainBoard: Fix USB connectors, ROUTED
    [RBCX-MainBoard.brd, RBCX-MainBoard.sch]
2020-05-07 MainBoardBRD: Fix DRC errors
    [RBCX-MainBoard.brd]
2020-05-07 MainBoardBRD: Add isolation cutout polygon around analog ground vias
    [RBCX-MainBoard.brd, RBCX-MainBoard.sch]
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2020-05-07 MainBoard: Fix microUSB pinout, add some tSilk
    [RBCX-MainBoard.brd, RBCX-MainBoard.sch]
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2020-05-08 MainBoardBRD: Add bottom silkscreen and improve top silkscreen
    [RBCX-MainBoard.brd, RBCX-MainBoard.sch]
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2020-05-09 MainBoard: fix motors signals, improve silkscreen
    - fix JST connector layout for M1 and M2
    - switch all pins to be compatible with chines motors with encoders
    - switch encoders signal on the coprocessor
    - fix direction/position of silkscreen text
    - move some vias due to silkscreen
    - add `esp32.lbr` library
    - improve silkscreen in `esp32.lbr` and `CR2032-circle.lbr` to fit on RBCX
    [RBCX-MainBoard.brd, RBCX-MainBoard.sch]
2020-05-09 ele/hw: clean and refactor project structure
    - rename folder `ele` to `hw`
    - remove folder `MainBoard`
    - to folder `hw` add folders `lib`,`configuration` and `designBlock`
    - rename `RBCX-MainBoard{.brd/.sch}` to `RBCX{.brd/.sch}`
    [RBCX.brd, RBCX.sch, parts.xlsx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]
2020-05-11 hw: Add default V resistors, fix polygon Q1, prepare manufacturing data
    - add 0R resistors as default voltage selector for SJx
    - improve size of polygon for Q1 due to better cooling
    - prepare manufacturing data
    - renumber parts in schema
    - create `parts_SMT.xlsx` file with updated data
    - add CAM processor configuration
    [RBCX.brd, RBCX.sch, parts (not updated).xlsx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]
2020-05-11 MainBoardBRD: Add tooling holes, required by JLCPCB SMT assembly
    [RBCX.brd]
2020-05-11 MainBoardBRD: Add placeholder text for JLCPCB order number
    [RBCX.brd]
2020-05-11 MainBoardBRD: Rotate some packages in libraries to match JLCPCB orientation
    [RBCX.brd, RBCX.sch]
2020-05-11 MainBoard: Swap PWM3A and PWM3B to maintain consistency
    [RBCX.brd, RBCX.sch]
2020-05-11 MainBoard: Fix pinout.xlsx and STM32F103VCTx.ioc
    [pinout.xlsx]
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2020-05-11 MainBoard: Swap encoders power polarity
    [RBCX.brd, RBCX.sch]
2020-05-11 hwBRD: Improve silkscreen
    - silkscreen: fix motors JST connectors VCC/GND, update communication connectors
    - modify silkscreen of ESP32-DEVKITC in library `esp32.lbr`
    [RBCX.brd, RBCX.sch]
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2020-05-13 Revert DRV8833-PWM-test
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2020-05-18 Fix frame buffer size, hide ControlLink symbols from linker
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2020-05-19 hwBRD: Fix power MOSFETs orientation
    [RBCX.brd, RBCX.sch]
2020-05-19 hwBRD: Fix SPI_SS3 and IN3 overlap
    [RBCX.brd]
2020-05-19 hwBRD: Fix R47 misplacement
    [RBCX.brd]
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2020-06-06 hwBRD: Replace buttons with SMD ones
    [RBCX.brd, RBCX.sch]
2020-06-06 hw: update pinhead library
    - update pinhead library in RBCX design and modify the XML in `RBCX{.brp/.sch}` for correct import to KiCad
    [RBCX.brd, RBCX.sch]
2020-06-06 Fix button order
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2020-06-07 Fix static initialization of FreeRTOS primitives
    [Dispatcher.cpp, main.cpp]
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2020-06-11 Fix yielding from ISR, call initPins earlier
    [DebugLink.cpp, main.cpp]
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2020-06-11 hw: fix clearence of SERVO3 and SERVO4 near bulk-caps
    [RBCX.brd]
2020-06-11 hw: fix power circuit capacitors value
    [RBCX.brd, RBCX.sch]
2020-06-11 hw: fix power button function without battery connected (only in schematic)
    [RBCX.brd, RBCX.sch]
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2020-06-12 hw: add middle battery voltage (with overvoltage protection) to the power input terminal block (replaced by 3-pin)
    [RBCX.brd, RBCX.sch]
2020-06-13 Fix unsol. status generation, use one-pulse mode for UTS
    [Dispatcher.cpp]
2020-06-14 Fix CdcUartTunnel, implement ESP32 boot sequences
    [Bsp.cpp, Bsp.hpp, Esp32Manager.cpp]
2020-06-15 hw: fix schematic related issues
    [RBCX.brd, RBCX.sch]
2020-06-15 hw: swap button 3 and 4, routing
    [RBCX.brd, RBCX.sch, pinout.xlsx]
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2020-06-15 Add utsIndex to CoprocStat message, fix first uts measurement
    [Bsp.cpp, Bsp.hpp]
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2020-06-16 Do not call DeInit in pinInit by default (fixes powering on)
    [Bsp.hpp, Esp32Manager.cpp]
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2020-06-17 hw: replace GND_SEPARATOR with cutout polygon
    [RBCX.brd]
2020-06-17 hw: fix polygons and GND testpoint
    [RBCX.brd, RBCX.sch]
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2020-06-17 hw: minor fixes
    [RBCX.brd]
2020-06-17 hw: add USB-C auxiliary signals connector and soldering pads around USB connectors for better fixation
    [RBCX.brd, RBCX.sch]
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2020-06-17 hw: replace output terminal box with ones from in-repo library
    [RBCX.brd, RBCX.sch]
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2020-06-17 hw: fix value of R74
    [RBCX.brd, RBCX.sch]
2020-06-18 hw: replace D1 with smaller one (SS34 -> B5819W)
    [RBCX.brd, RBCX.sch]
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2020-06-18 hw: fix ESP32 DevKit C silkscreen
    - activate "Spin" for all text labels in DEVKITC footprint
    [RBCX.brd, RBCX.sch]
2020-06-19 hw: update and fix silkscreens
    - fix position of labels
    - add testpoint labels
    - improve groups of text (separate columns in text labels)
    - add label for capacitors polarity
    - change layer from `tDocu` to `Document` for label in library `switch-omron.lbr`
    [RBCX.brd, RBCX.sch]
2020-06-20 Fix debug IRQ prio
    [Bsp.hpp]
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2020-06-21 hw: change outline layer of display modules
    - `diy-modules.lbr` - change outline layer from `tPlace` to `Document`
    - footprint `DISPLAY-OLED-128X32`
    - footprint `DISPLAY-OLED-128X64-I2C_W-HOLES`
    [RBCX.brd, RBCX.sch]
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2020-06-22 hw: fix position of origin in default jumper footprint
    - library `jumper.lbr` - `SJ2W_DEFAULT` - fix position of origin
    - update `RBCX.brd`
    [RBCX.brd, RBCX.sch]
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2020-06-22 hw: change size of holes for USBC connector
    - library `USB.lbr`
    - footprint `USB_C_8PIN` - change holes size from 0.35 mm to 0.30 mm to fit JLCPCB requirements
    [RBCX.brd, RBCX.sch]
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2020-07-03 Handle missing fw_ version tag
    [pre_generate_version_defines.py]
2020-07-05 hw: Release/manufacture version 1.1
    Summary:
    - fix USB-C connector - footprint `USB_C_8PIN` - change holes size from 0.35 mm to 0.30 mm to fit JLCPCB requirements
    - add USB-C auxiliary signals connector and soldering pads around USB connectors for better fixation
    - remove bottom mask and fix stop mask under DRV8833s centre pad
    - modify jumpers to match 0603 resistors size
    - fix position of origin in default jumper footprint for correct SMT
    - move bottom LED resistors to the top
    - add middle battery voltage (with over voltage protection) to the power input terminal block (replaced by 3-pin)
    - remove resistor between STM and ESP enable
    - change pinouts for buttons
    - replace buttons with SMD on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
    [RBCX.brd, RBCX.sch, pinout.xlsx]
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2020-07-05 Fix Queue and MessageBuffer wrapper's ISR yield handling
    [DebugLink.cpp, Dispatcher.cpp]
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2020-07-07 Do not trigger ESP32 watchdog when held in reset
    [Esp32Manager.cpp]
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2020-07-09 Handle USB events in IRQ rather than polling
    * The main loop is too slow for Windows drivers due to control
    messages decoding taking too long.
    [Bsp.cpp, Bsp.hpp, Esp32Manager.cpp]
2020-07-09 Raise priority to prevent USB IRQ from racing with usb_ep_read/write
    [Bsp.hpp]
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2020-07-11 Auto-reset RBCX into DFU on sboot upload
    [post_dfu.py]
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2020-07-11 Fix debug uart detection
    * The pullup capacitor is slow to charge up, force it
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2020-07-11 Fix post_dfu.py on Windows
    [post_dfu.py]
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2020-07-13 Fix debug position call
    [DebugLink.cpp]
2020-07-13 Fix member initialization in Motor
2020-07-14 Use explicit reset() instead of Motor construction at soft reset
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2020-09-19 hw: change resistors R20 - R23 valu to 2k2 (VUSB and ESP_+5V power LED resistors)
    [RBCX.brd, RBCX.sch]
2020-09-19 hw: disconnect 3V3_EN and D11 (this connection prevents main step-down IM1 from startup)
    [RBCX.brd, RBCX.sch]
2020-09-19 hw: fix jst connectors drill (motor connectors) and pad size (iServo connectors), move bottom pinheads to left to make enough space for iServo connectors
    [RBCX.brd, RBCX.sch]
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2020-10-11 hw: add two small areas of unmasked GND plane for oscilloscope clip
    [RBCX.brd]
2020-10-11 hw: fixed iLed silkscreen
    [RBCX.brd]
2020-10-12 hw: fix USB-C CC pin pull-down resistors value.
    [RBCX.brd, RBCX.sch]
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2020-10-12 hw: fix tNames
    [RBCX.brd, RBCX.sch]
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2020-10-12 hw: fix D1 symbol
    [RBCX.brd, RBCX.sch]
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2020-10-12 hw: fix encoders pull-up resistors value
    [RBCX.brd, RBCX.sch]
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2021-04-19 Revert velocity ramping motor changes
    They did not work well in real-world testing and we want the master
    to be useable.
    This reverts commit ca02e360475b70f186cf4639121ef47abeeff4ba.
    This reverts commit 5b80842b56ccd478ef0caa50ece7596251d0460a.
    This reverts commit d5262ff970676f4caf6ee55bf52c5202b1f619d8.
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2021-05-02 Fix I2C devAddress
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2021-05-11 Add I2C error handler
    [I2cController.cpp]
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2021-07-23 Fix ESP reset by change i2c queue timeout, add i2c reset
    [Bsp.cpp, I2cController.cpp, I2cController.hpp]
2021-07-26 Add i2c error message
    [I2cController.cpp]
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2021-07-27 Fix MPU timer reinit
    [Bsp.cpp, DebugLink.cpp, I2cController.cpp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]
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

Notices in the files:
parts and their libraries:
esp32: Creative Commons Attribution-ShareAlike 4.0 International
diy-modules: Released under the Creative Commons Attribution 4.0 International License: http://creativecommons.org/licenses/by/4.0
